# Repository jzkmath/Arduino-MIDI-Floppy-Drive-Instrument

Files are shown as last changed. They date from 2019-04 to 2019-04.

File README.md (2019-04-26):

# Arduino MIDI Floppy Drive Instrument

This is the design files for an Arduino Floppy-Drive controller that is MIDI Controlled.
It is a combination of the [MIDI Stepper Synth V1](https://github.com/jzkmath/Arduino-MIDI-Stepper-Motor-Instrument) and [Moppy Software](https://github.com/SammyIAm/Moppy2).

The core method for controlling the floppy drives is the use of a non-blocking delay. If you want to make a stepper motor play at a certain frequency, simply pulse the pin at that specified frequency. In this case however, the position of the drive head is important, so we simply need to track the position and reverse direction when that point is reached.

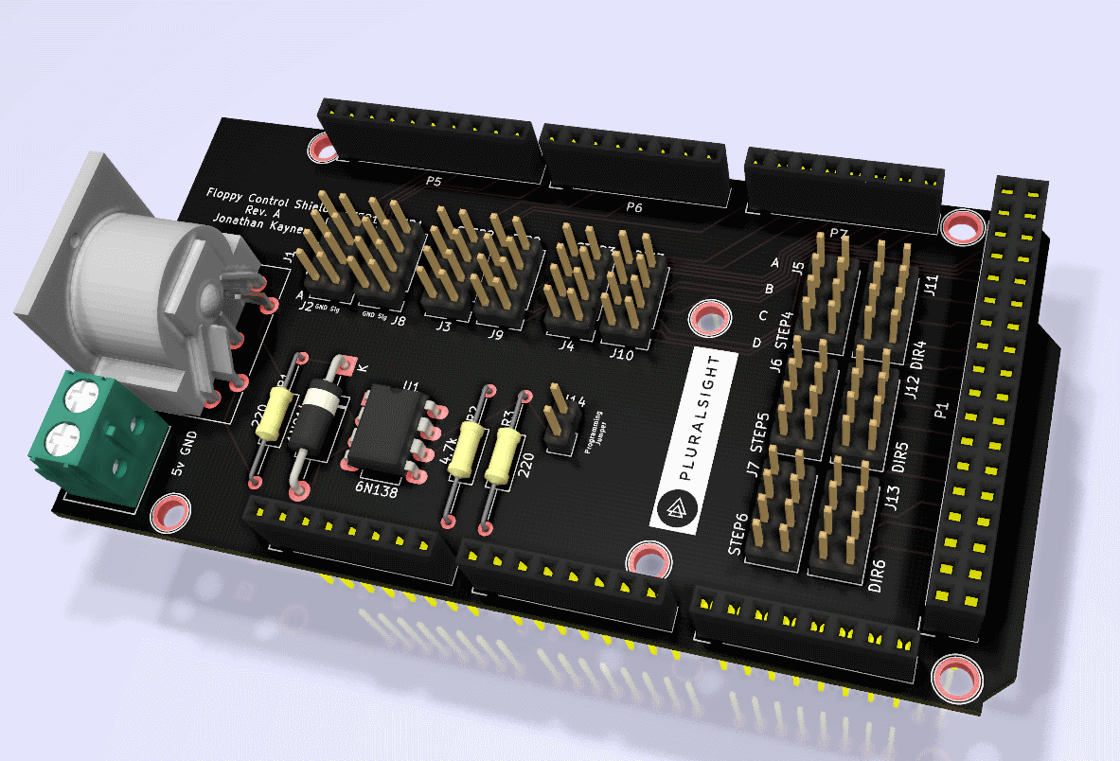
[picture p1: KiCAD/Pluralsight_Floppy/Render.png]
PCB Render


Refer to the schematic for pinouts. The header pins connect to the IDE connector of the floppy drive and maintain the ground reference.

Look at this pinout:

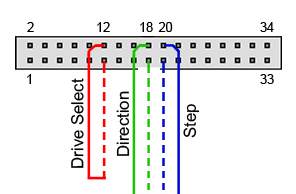
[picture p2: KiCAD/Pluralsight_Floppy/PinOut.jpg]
IDE Pinout


We need to connect "drive select" together (Pins 11 and 12) to enable the drive and then connect the Step and Direction to the Shield. 

### PINOUT:
12 - Drive Select (Enable)

11 - Drive Select Ground

18 - Direction

17 - Direction Ground

20 - Step

19 - Step Ground

## NOTE:
There is a two pin header (J14) that is the programming jumper. The jumper should be installed here and removed when the Arduino is being programmed. This is because the MIDI Rx line is also use to program the Arduino when its being flashed.

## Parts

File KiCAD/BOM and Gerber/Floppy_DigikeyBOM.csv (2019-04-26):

Manufacturer Part Number | Manufacturer | Digi-Key Part Number | Customer Reference | Reference Designator | Packaging | Part Status | Quantity | Unit Price | Extended Price | Quantity Available | Mfg Std Lead Time | Description | RoHS Status | Lead Free Status | REACH Status | US Tariff Status
1N914 | ON Semiconductor | 1N914FS-ND |  |  | Bulk | Active | 1 | 0.10000 | $0.10 | 50098 | 17 Weeks | DIODE GEN PURP 100V 200MA DO35 | RoHS Compliant | Lead free | REACH Unaffected | Tariff Applied
SDS-50J | CUI Inc. | CP-2350-ND |  |  | Tray | Active | 1 | 1.96000 | $1.96 | 24520 | 14 Weeks | CONN RCPT FMALE DIN 5POS SOLDER | RoHS Compliant | Lead free | Not Available | Tariff Applied
61300821121 | Wurth Electronics Inc. | 732-5296-ND |  |  | Bag | Active | 12 | 0.55700 | $6.68 | 4368 | 14 Weeks | CONN HEADER VERT 8POS 2.54MM | RoHS Compliant | Lead free | REACH Unaffected
61300211121 | Wurth Electronics Inc. | 732-5315-ND |  |  | Bag | Active | 1 | 0.13000 | $0.13 | 150130 | 14 Weeks | CONN HEADER VERT 2POS 2.54MM | RoHS Compliant | Lead free | REACH Unaffected
OSTTA020161 | On Shore Technology Inc. | ED2561-ND |  |  | Bulk | Active | 1 | 0.69000 | $0.69 | 16564 | 12 Weeks | TERM BLK 2POS SIDE ENTRY 5MM PCB | RoHS Compliant | Lead free | REACH Unaffected | Tariff Applied
61303621121 | Wurth Electronics Inc. | 732-5309-ND |  |  | Bag | Active | 1 | 1.72000 | $1.72 | 999 | 14 Weeks | CONN HEADER VERT 36POS 2.54MM | RoHS Compliant | Lead free | REACH Unaffected
61300811121 | Wurth Electronics Inc. | 732-5321-ND |  |  | Bag | Active | 5 | 0.37000 | $1.85 | 16954 | 14 Weeks | CONN HEADER VERT 8POS 2.54MM | RoHS Compliant | Lead free | REACH Unaffected
61301011121 | Wurth Electronics Inc. | 732-2670-ND |  |  | Bag | Active | 1 | 0.89000 | $0.89 | 2109 | 14 Weeks | CONN HEADER VERT 10POS 2.54MM | RoHS Compliant | Lead free | REACH Unaffected
CFM14JT220R | Stackpole Electronics Inc | S220QCT-ND |  |  | Cut Tape (CT) | Active | 2 | 0.10000 | $0.20 | 32976 | 15 Weeks | RES 220 OHM 1/4W 5% CF MINI | RoHS Compliant | Lead free | REACH Unaffected | Tariff Applied
CFM14JT4K70 | Stackpole Electronics Inc | S4.7KQCT-ND |  |  | Cut Tape (CT) | Active | 1 | 0.10000 | $0.10 | 65656 | 15 Weeks | RES 4.7K OHM 1/4W 5% CF MINI | RoHS Compliant | Lead free | REACH Unaffected | Tariff Applied
6N138 | Lite-On Inc. | 160-1795-ND |  |  | Tube | Active | 1 | 0.81000 | $0.81 | 3824 | 10 Weeks | OPTOISO 5KV DARL W/BASE 8DIP | RoHS Compliant | Lead free | Not Available
A 08-LC-TT | Assmann WSW Components | AE9986-ND |  |  | Tube | Active | 1 | 0.18000 | $0.18 | 98790 | 20 Weeks | CONN IC DIP SOCKET 8POS TIN | RoHS Compliant | Lead free | REACH Unaffected | Tariff Eligible
QPC02SXGN-RC | Sullins Connector Solutions | S9337-ND |  |  | Bag | Active | 1 | 0.10000 | $0.10 | 553226 | 5 Weeks | CONN JUMPER SHORTING .100" GOLD | RoHS Compliant | Lead free | REACH Unaffected

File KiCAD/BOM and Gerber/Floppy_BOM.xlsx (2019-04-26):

Qty | Reference(s) | Value | Digikey PN | Price ea | Final Price | Final Price: | $16.65
1 | D1 | 1N914 | 1N914FS-ND (https://www.digikey.com/short/pch9zj) | $0.10 | $0.10
1 | J1 | MIDI DIN Connector | CP-2350-ND (https://www.digikey.com/short/pch9p7) | $1.96 | $1.96
12 | J2 - J13 | 2x4 Header | 732-5296-ND (https://www.digikey.com/short/pzchtq) | $0.66 | $7.92
1 | J3 | 1x2 Header | 732-5315-ND (https://www.digikey.com/short/ppd0ct) | $0.13 | $0.13
1 | J4 | 2 Pos Screw Term | ED2561-ND (https://www.digikey.com/short/pq31n1) | $0.69 | $0.69
1 | P1 | 2x18 Header | 732-5309-ND (https://www.digikey.com/short/ppddd2) | $1.72 | $1.72
5 | P2, P3, P4, P6, P7 | 1x8 Header | 732-5321-ND (https://www.digikey.com/short/ppddr3) | $0.37 | $1.85
1 | P5 | 1x10 Header | 732-2670-ND (https://www.digikey.com/short/ppd035) | $0.89 | $0.89
2 | R1, R3 | 220 | S220QCT-ND (https://www.digikey.com/short/ppbfp4) | $0.10 | $0.20
1 | R2 | 4.7k | S4.7KQCT-ND (https://www.digikey.com/short/ppbfp0) | $0.10 | $0.10
1 | U3 | 6N138 | 160-1795-ND (https://www.digikey.com/short/pch9pf) | $0.81 | $0.81
1 | U3 | DIP8 Socket | AE9986-ND (https://www.digikey.com/short/pch9mn) | $0.18 | $0.18
1 | J3 | Jumper | S9337-ND (https://www.digikey.com/short/ppd0wj) | $0.10 | $0.10
 |  |  |  |  | $0.00
 |  |  |  |  | $0.00
 |  |  |  |  | $0.00
 |  |  |  |  | $0.00
 |  |  |  |  | $0.00
 |  |  |  |  | $0.00
 |  |  |  |  | $0.00
 |  |  |  |  | $0.00
 |  |  |  |  | $0.00
 |  |  |  |  | $0.00
 |  |  |  |  | $0.00
 |  |  |  |  | $0.00
 |  |  |  |  | $0.00
 |  |  |  |  | $0.00
 |  |  |  |  | $0.00
 |  |  |  |  | $0.00
 |  |  |  |  | $0.00
 |  |  |  |  | $0.00
 |  |  |  |  | $0.00
 |  |  |  |  | $0.00

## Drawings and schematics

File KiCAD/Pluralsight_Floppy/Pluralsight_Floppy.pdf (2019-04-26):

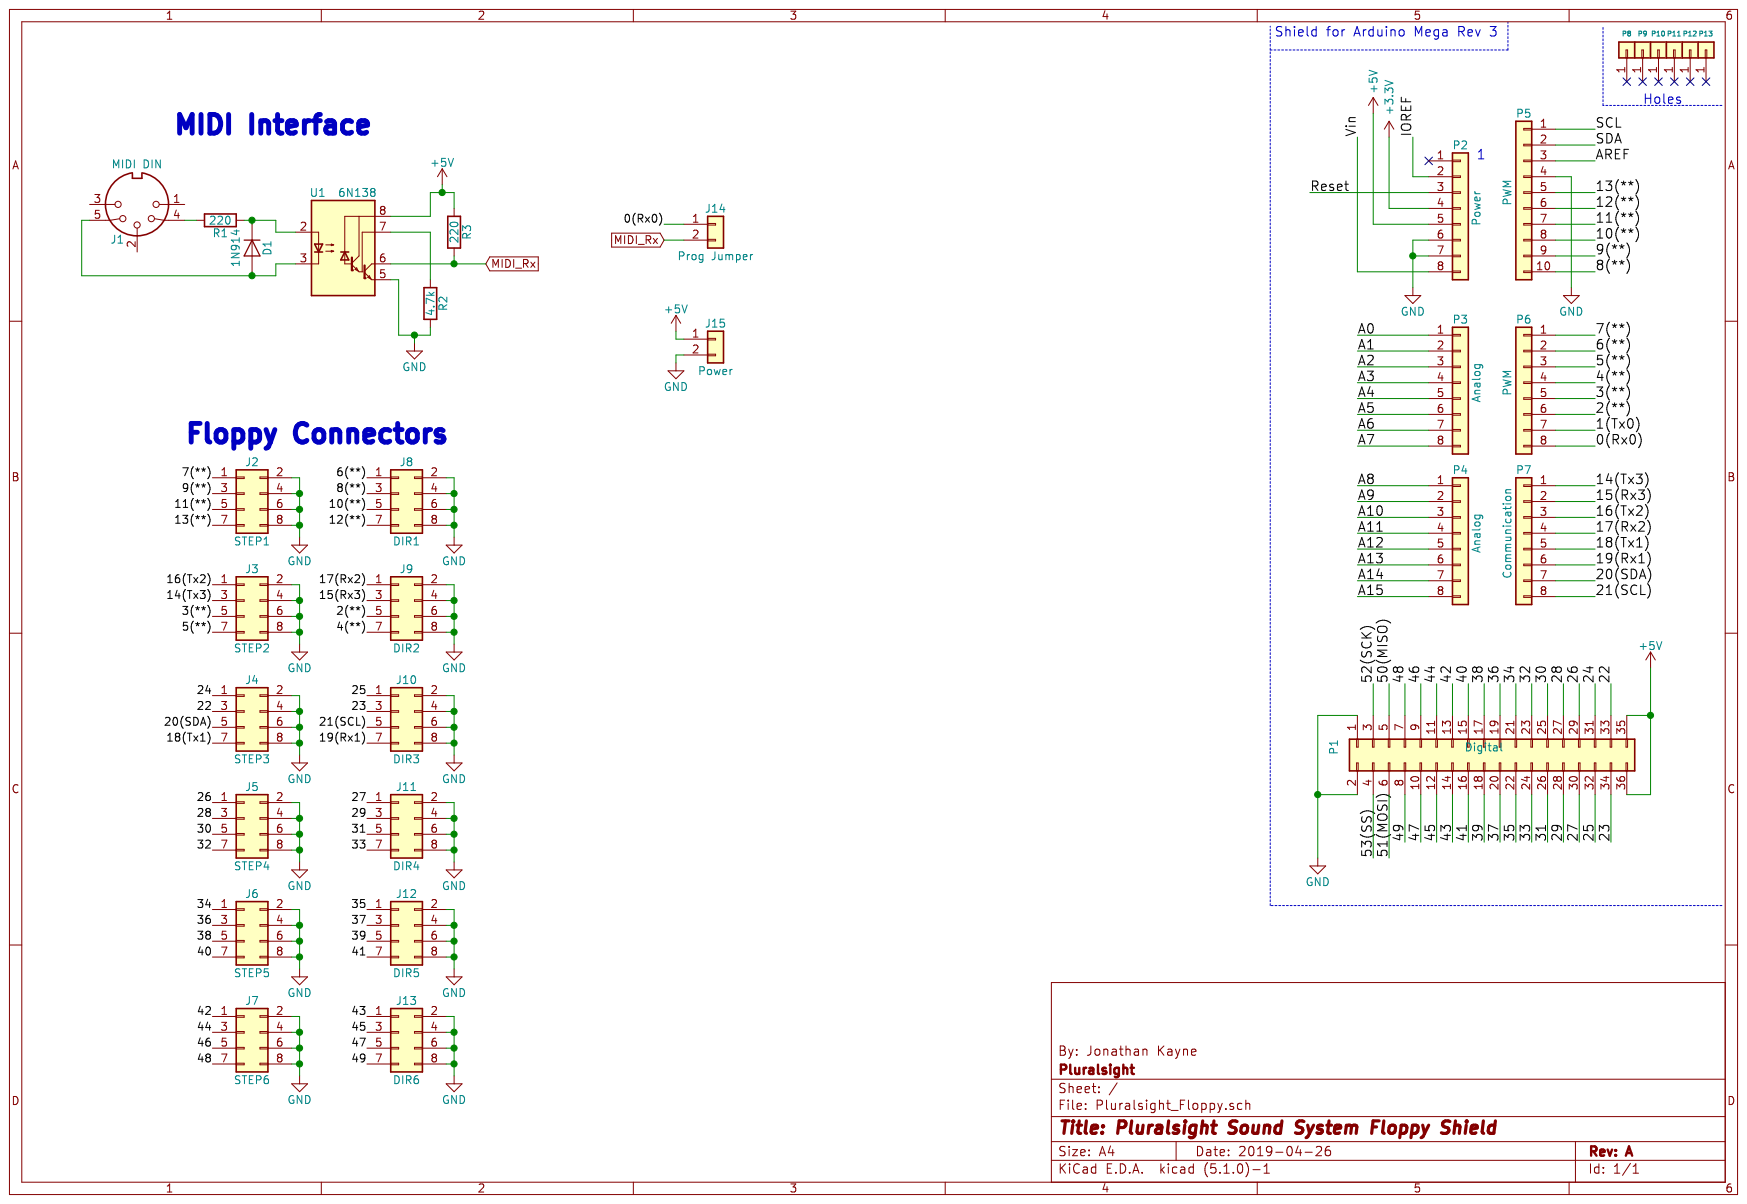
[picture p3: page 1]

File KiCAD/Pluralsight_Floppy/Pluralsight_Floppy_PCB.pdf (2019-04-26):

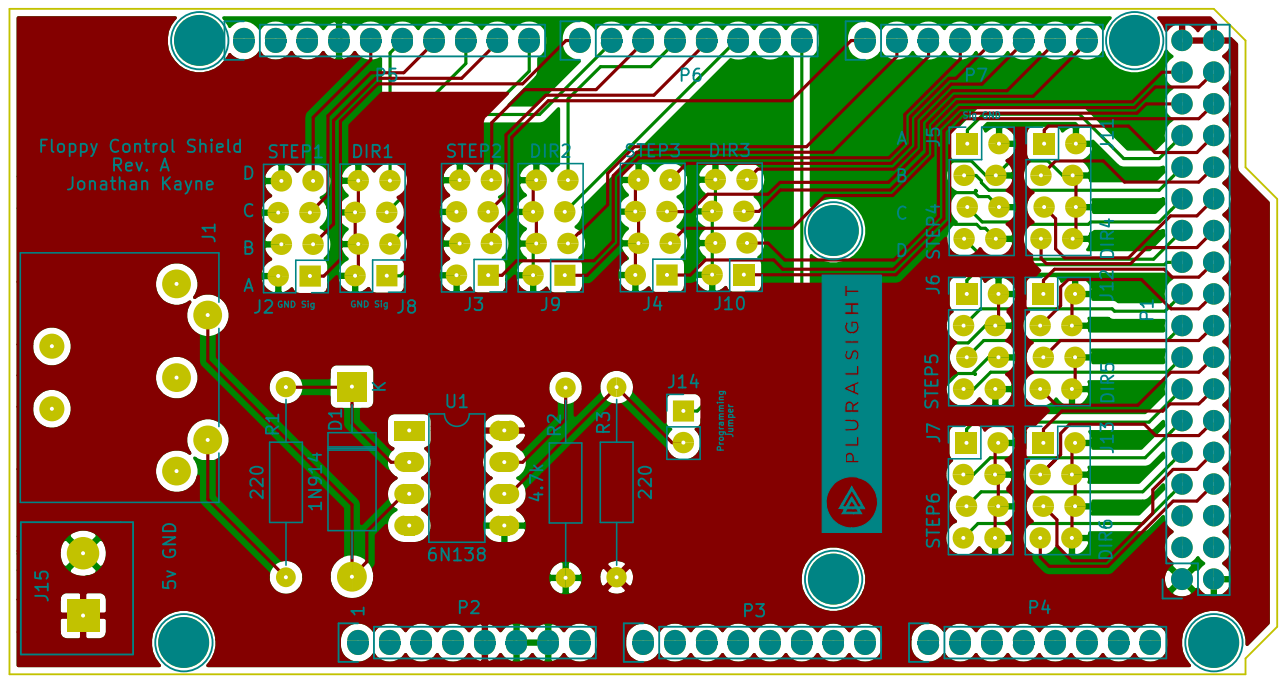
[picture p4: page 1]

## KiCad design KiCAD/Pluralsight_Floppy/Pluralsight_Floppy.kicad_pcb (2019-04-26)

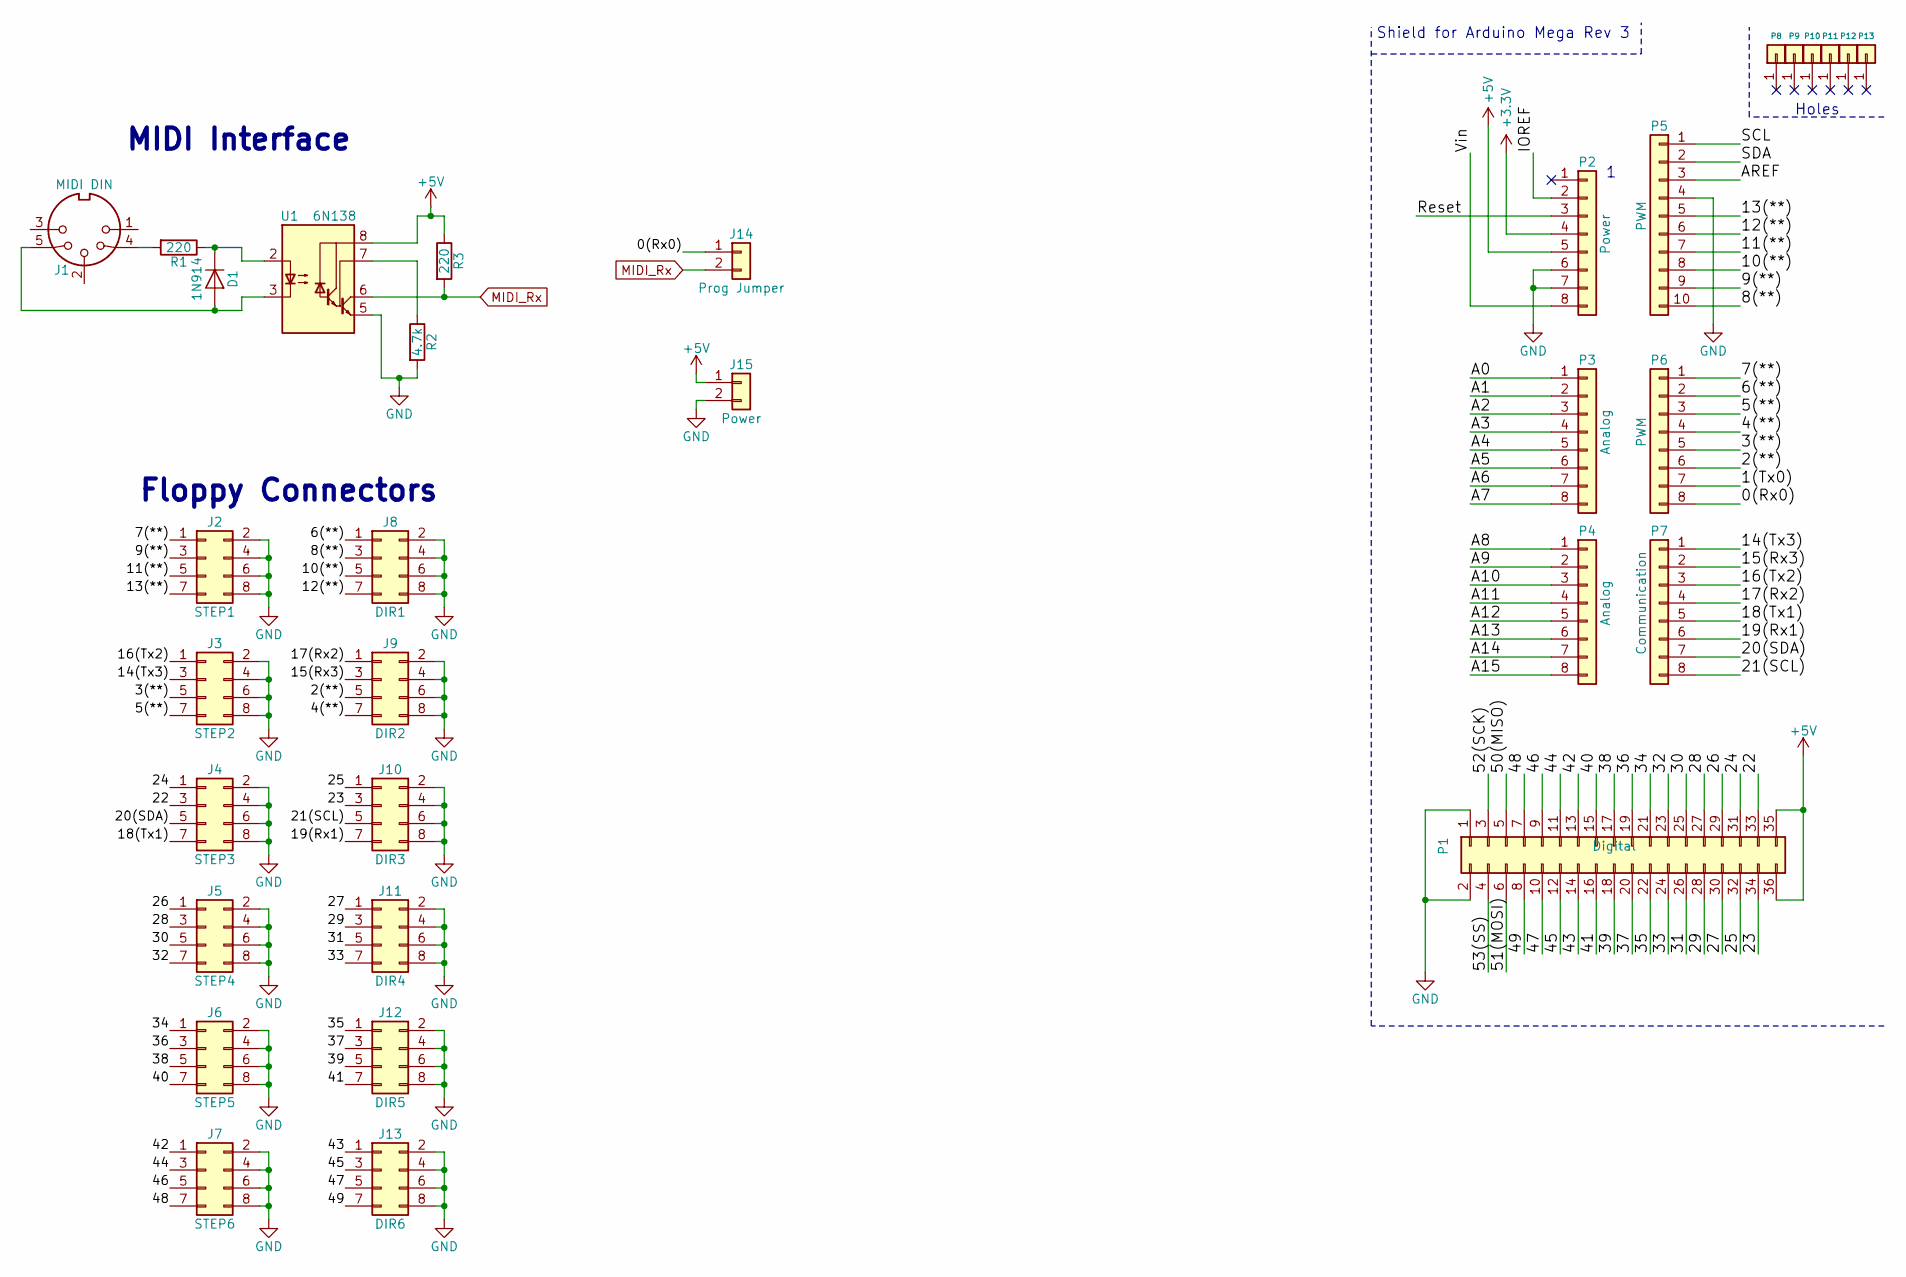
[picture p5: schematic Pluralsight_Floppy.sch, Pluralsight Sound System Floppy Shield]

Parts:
D1: 1N914; D_DO-15_P15.24mm_Horizontal
J1: MIDI DIN; SDS-50J
J2: STEP1; PinHeader_2x04_P2.54mm_Vertical_zigzag
J3: STEP2; PinHeader_2x04_P2.54mm_Vertical_zigzag
J4: STEP3; PinHeader_2x04_P2.54mm_Vertical_zigzag
J5: STEP4; PinHeader_2x04_P2.54mm_Vertical_zigzag
J6: STEP5; PinHeader_2x04_P2.54mm_Vertical_zigzag
J7: STEP6; PinHeader_2x04_P2.54mm_Vertical_zigzag
J8: DIR1; PinHeader_2x04_P2.54mm_Vertical_zigzag
J9: DIR2; PinHeader_2x04_P2.54mm_Vertical_zigzag
J10: DIR3; PinHeader_2x04_P2.54mm_Vertical_zigzag
J11: DIR4; PinHeader_2x04_P2.54mm_Vertical_zigzag
J12: DIR5; PinHeader_2x04_P2.54mm_Vertical_zigzag
J13: DIR6; PinHeader_2x04_P2.54mm_Vertical_zigzag
J14: Prog Jumper; PinHeader_1x02_P2.54mm_Vertical
J15: Power; 2_Pos_Screw_Term
P1: Digital; Socket_Strip_Arduino_2x18
P2: Power; Socket_Strip_Arduino_1x08
P3, P4: Analog; Socket_Strip_Arduino_1x08
P5: PWM; Socket_Strip_Arduino_1x10
P6: PWM; Socket_Strip_Arduino_1x08
P7: Communication; Socket_Strip_Arduino_1x08
P8, P9, P10, P11, P12, P13: CONN_01X01; Arduino_1pin
R1, R3: 220; R_Axial_DIN0207_L6.3mm_D2.5mm_P15.24mm_Horizontal
R2: 4.7k; R_Axial_DIN0207_L6.3mm_D2.5mm_P15.24mm_Horizontal
U1: 6N138; DIP-8_W7.62mm_LongPads

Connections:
+3V3: P2.4
+5V: J15.1, P1.35, P1.36, P2.5, R3.1, U1.8 (VCC)
/0(Rx0): J14.1, P6.8
/1(Tx0): P6.7
/2(**): J9.5, P6.6
/3(**): J3.5, P6.5
/4(**): J9.7, P6.4
/5(**): J3.7, P6.3
/6(**): J8.1, P6.2
/7(**): J2.1, P6.1
/8(**): J8.3, P5.10
/9(**): J2.3, P5.9
/10(**): J8.5, P5.8
/11(**): J2.5, P5.7
/12(**): J8.7, P5.6
/13(**): J2.7, P5.5
/14(Tx3): J3.3, P7.1
/15(Rx3): J9.3, P7.2
/16(Tx2): J3.1, P7.3
/17(Rx2): J9.1, P7.4
/18(Tx1): J4.7, P7.5
/19(Rx1): J10.7, P7.6
/20(SDA): J4.5, P7.7
/21(SCL): J10.5, P7.8
/22: J4.3, P1.33
/23: J10.3, P1.34
/24: J4.1, P1.31
/25: J10.1, P1.32
/26: J5.1, P1.29
/27: J11.1, P1.30
/28: J5.3, P1.27
/29: J11.3, P1.28
/30: J5.5, P1.25
/31: J11.5, P1.26
/32: J5.7, P1.23
/33: J11.7, P1.24
/34: J6.1, P1.21
/35: J12.1, P1.22
/36: J6.3, P1.19
/37: J12.3, P1.20
/38: J6.5, P1.17
/39: J12.5, P1.18
/40: J6.7, P1.15
/41: J12.7, P1.16
/42: J7.1, P1.13
/43: J13.1, P1.14
/44: J7.3, P1.11
/45: J13.3, P1.12
/46: J7.5, P1.9
/47: J13.5, P1.10
/48: J7.7, P1.7
/49: J13.7, P1.8
/50(MISO): P1.5
/51(MOSI): P1.6
/52(SCK): P1.3
/53(SS): P1.4
/A0: P3.1
/A1: P3.2
/A2: P3.3
/A3: P3.4
/A4: P3.5
/A5: P3.6
/A6: P3.7
/A7: P3.8
/A8: P4.1
/A9: P4.2
/A10: P4.3
/A11: P4.4
/A12: P4.5
/A13: P4.6
/A14: P4.7
/A15: P4.8
/AREF: P5.3
/IOREF: P2.2
/Reset: P2.3
/SCL: P5.1
/SDA: P5.2
/Vin: P2.8
GND: J2.2, J2.4, J2.6, J2.8, J3.2, J3.4, J3.6, J3.8, J4.2, J4.4, J4.6, J4.8, J5.2, J5.4, J5.6, J5.8, J6.2, J6.4, J6.6, J6.8, J7.2, J7.4, J7.6, J7.8, J8.2, J8.4, J8.6, J8.8, J9.2, J9.4, J9.6, J9.8, J10.2, J10.4, J10.6, J10.8, J11.2, J11.4, J11.6, J11.8, J12.2, J12.4, J12.6, J12.8, J13.2, J13.4, J13.6, J13.8, J15.2, P1.1, P1.2, P2.6, P2.7, P5.4, R2.2, U1.5 (GND)
MIDI_Rx: J14.2, R3.2, U1.6 (VO2)
unnamed: D1.1 (K), R1.1, U1.2 (C1)
unnamed: D1.2 (A), J1.5, U1.3 (C2)
unnamed: J1.4, R1.2
unnamed: R2.1, U1.7 (VO1)

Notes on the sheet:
Shield for Arduino Mega Rev 3
Holes
MIDI Interface
Floppy Connectors

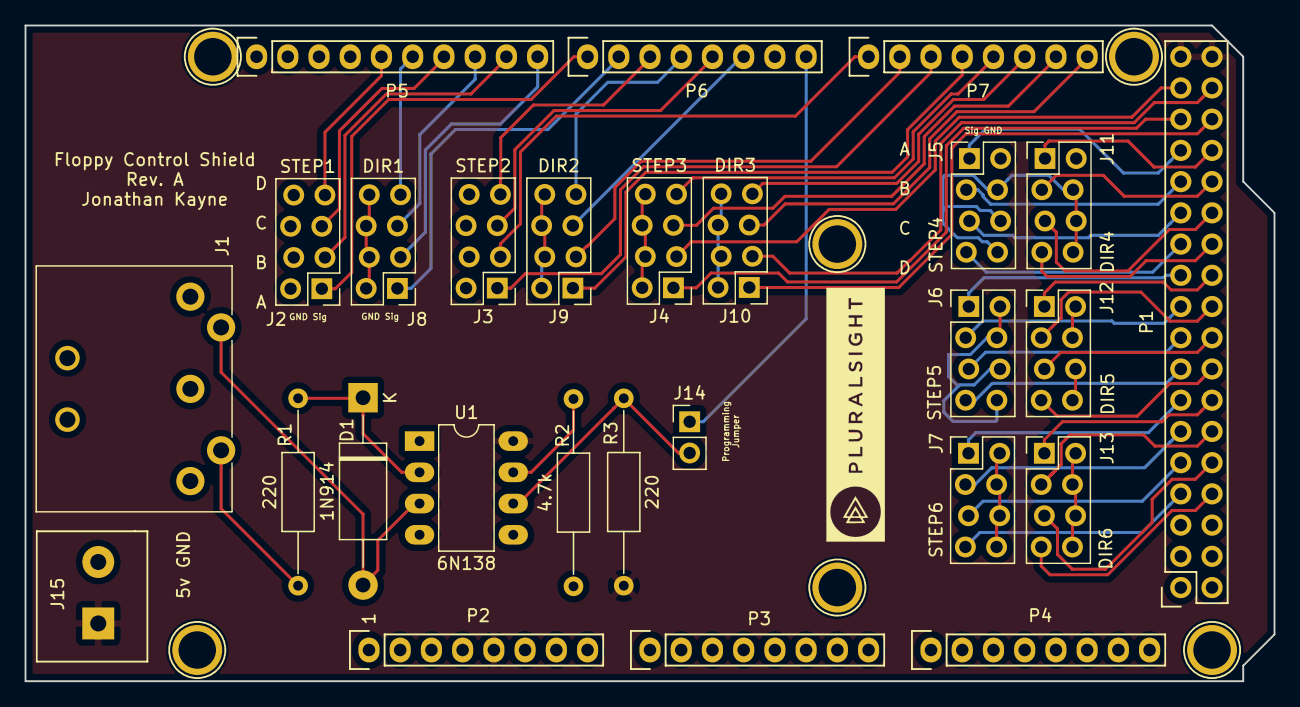
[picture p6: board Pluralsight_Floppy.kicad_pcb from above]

Board: 2 copper layers, 101.6 x 53.3 mm, 33 parts (0 on the bottom side), 56 nets.

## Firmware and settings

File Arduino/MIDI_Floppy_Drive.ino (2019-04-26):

#include <MIDI.h>
#include "pitches.h"

/*
 * MIDI FLOPPY DRIVE SYNTH
 * By: Jonathan Kayne, 2019
 * 
 * Modified version of the Moppy Software and the MIDI Stepper Synth V1
 * that drives 24 floppy drives.
 * The main difference is that we need to track the position of the stepper motors
 * so direction becomes important.
 * 
 * This is configured for 24 floppy drives and 4 per channel
 */

#define MAX_POS 80 //3.5" = 80, 5.25" = 50
#define NUM_DRIVES 24

// PINS
const long floppyStepPins[] = {7, 9, 11, 13, 16, 14, 3, 5, 24, 22, 20, 18, 26, 28, 30, 32, 34, 36, 38, 40, 42, 44, 46, 48}; //step pins of the floppy drives
const long floppyDirPins[] = {6, 8, 10, 12, 17, 15, 2, 4, 25, 23, 21, 19, 27, 29, 31, 33, 35, 37, 39, 41, 43, 45, 47, 49}; //direction pins of the floppy drives

// CURRENT LOCATION
unsigned long floppyPos[] = {0, 0, 0, 0, 0, 0, 0, 0, 0, 0, 0, 0, 0, 0, 0, 0, 0, 0, 0, 0, 0, 0, 0, 0}; //the current position of the floppy drive
bool floppyDir[] = {0, 0, 0, 0, 0, 0, 0, 0, 0, 0, 0, 0, 0, 0, 0, 0, 0, 0, 0, 0, 0, 0, 0, 0}; //the current direction of the floppy drive

// SPEEDS
unsigned long motorSpeeds[] = {0, 0, 0, 0, 0, 0, 0, 0, 0, 0, 0, 0, 0, 0, 0, 0, 0, 0, 0, 0, 0, 0, 0, 0}; //holds the speeds of the motors.
unsigned long prevStepMicros[] = {0, 0, 0, 0, 0, 0, 0, 0, 0, 0, 0, 0, 0, 0, 0, 0, 0, 0, 0, 0, 0, 0, 0, 0}; //last time

MIDI_CREATE_DEFAULT_INSTANCE(); //use default MIDI settings

void setup() 
{
  for(int l = 0; l < NUM_DRIVES; l++) //set all pins as output
  {
    pinMode(floppyStepPins[l], OUTPUT);
    pinMode(floppyDirPins[l], OUTPUT);
  }

  resetFloppies(); //reset all floppy drives before initializing MIDI
  
  MIDI.begin(MIDI_CHANNEL_OMNI); //listen to all MIDI channels
  MIDI.setHandleNoteOn(handleNoteOn); //execute function when note on message is recieved
  MIDI.setHandleNoteOff(handleNoteOff); //execute function when note off message is recieved
}

void loop() 
{
  MIDI.read(); //read MIDI messages
  for (int k = 0; k < NUM_DRIVES; k++) //perform singleStep for all motors
  {
    singleStep(k);
  }
}

// Moves all the floppy drives to the home position
void resetFloppies()
{
  for (int i = 0; i < NUM_DRIVES; i++)
  {
    digitalWrite(floppyDirPins[i], HIGH); //go in reverse
    for (int j = 0; j < MAX_POS; j++)
    {
      digitalWrite(floppyStepPins[j], HIGH); //single step to lowest position
      digitalWrite(floppyStepPins[j], LOW);
      delay(5);
    }
  }
}

// Update motor speed based on Note and Velocity
void handleNoteOn(byte channel, byte pitch, byte velocity) //MIDI Note ON Command
{
  if (velocity > 0) //one motor
  {
    motorSpeeds[(channel * 4)] = pitchVals[pitch]; //set the motor speed to specified pitch
  }

  if (velocity >= 32) //two motors
  {
    motorSpeeds[(channel * 4) + 1] = pitchVals[pitch]; //set the motor speed to specified pitch
  }

  if (velocity >= 64) //three motors
  {
    motorSpeeds[(channel * 4) + 2] = pitchVals[pitch]; //set the motor speed to specified pitch
  }

  if ((velocity >= 96) && (velocity <= 127)) //four motors
  {
    motorSpeeds[(channel * 4) + 3] = pitchVals[pitch]; //set the motor speed to specified pitch
  }

}

// Set the motor speed of all four motors in a channel to zero
void handleNoteOff(byte channel, byte pitch, byte velocity) //MIDI Note OFF Command
{
  motorSpeeds[channel * 4] = 0; //set first motor speed to zero
  motorSpeeds[(channel * 4) + 1] = 0; //set second motor speed to zero
  motorSpeeds[(channel * 4) + 2] = 0; //set third motor speed to zero
  motorSpeeds[(channel * 4) + 3] = 0; //set fourth motor speed to zero
}

// Advance the floppy drive by 1 step when the time elapses
void singleStep(byte motorNum)
{
  if ((micros() - prevStepMicros[motorNum] >= motorSpeeds[motorNum]) && (motorSpeeds[motorNum] != 0))
  { //step when correct time has passed and the motor is at a nonzero speed

    //Switch directions if end has been reached
    if (floppyPos[motorNum] >= MAX_POS)
    {
      floppyDir[motorNum] = HIGH;
      digitalWrite(floppyDirPins[motorNum], HIGH);
    }
    else if (floppyPos[motorNum] <= 0)
    {
      floppyDir[motorNum] = LOW;
      digitalWrite(floppyDirPins[motorNum], LOW);
    }

    //Update current position of drive
    if (floppyDir[motorNum] == HIGH) 
    {
      floppyPos[motorNum]--;
    }
    else 
    {
      floppyPos[motorNum]++;
    }

    prevStepMicros[motorNum] += motorSpeeds[motorNum]; //update prev time
    digitalWrite(floppyStepPins[motorNum], HIGH); //pulse pin
    digitalWrite(floppyStepPins[motorNum], LOW);
  }
}

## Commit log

2019-04-26 Added KiCAD files
    [Floppy_BOM.xlsx, Floppy_DigikeyBOM.csv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]
2019-04-26 Added Arduino Code
